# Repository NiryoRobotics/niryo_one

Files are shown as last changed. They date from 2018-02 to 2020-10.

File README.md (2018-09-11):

# Niryo One

(Niryo One : [https://niryo.com](https://niryo.com/?utm_source=github))

Niryo One image

This repository contains STL files to print Niryo One with a 3D printer.

Note : **You need at least a 200mm\*200mm\*200mm 3D printer to be able to print all the parts.**

You can find Niryo One ROS stack here : https://github.com/NiryoRobotics/niryo_one_ros 

Enjoy !

---

Note : if you have received your Niryo One before September 2018, the files related to your robot are located in the "Archive (v 1.1.0)" folder.

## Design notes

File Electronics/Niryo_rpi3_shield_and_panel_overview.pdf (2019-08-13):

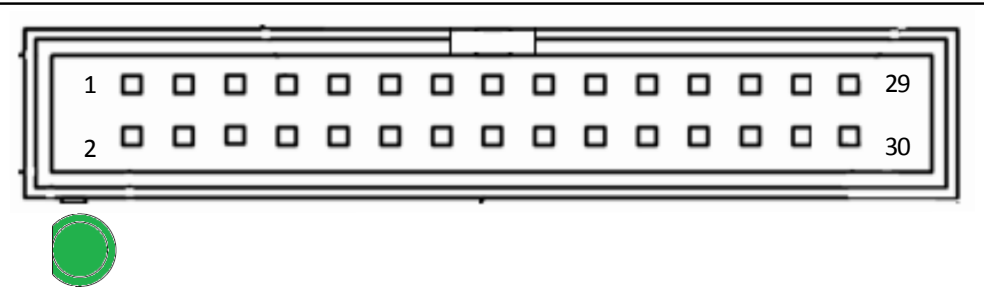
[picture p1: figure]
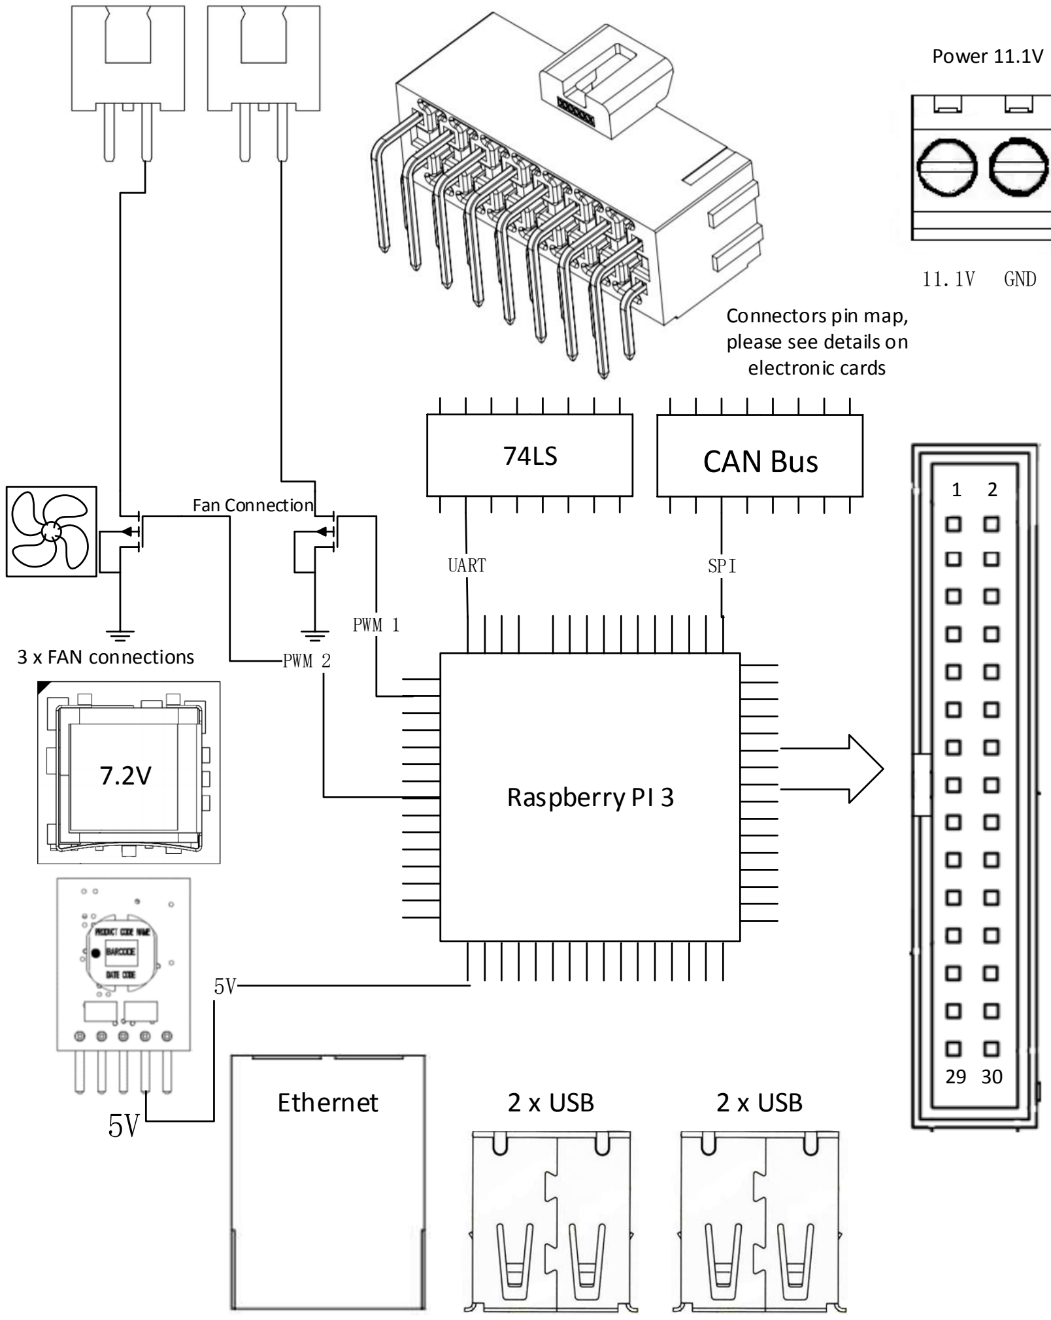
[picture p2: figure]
Raspberry PI 3; CAN Bus ⁷⁴LS; Power 11.1V; 3 x FAN connections; UART; SPI; PWM 2; PWM 1; GND; Fan Connection; Ethernet; 2 x USB; Connectors pin map, please see details on electronic cards

CANH CANL GND 11.1V | GND 7.2V DLX-Data1 | GND 11.1V
CANH CANL GND 11.1V | GND 11.1V

GND 5V 1A(IO2) 1B(IO3) 1C (IO16)

GND 5V 2A(IO26) 2B(IO19) 2C(IO6)
GND 7.2V DLX-Data2

NiryoShield Pin Map

Pin# | Name
01 | 7.2V DC Power
03 | DLX-Data
05 | 11.1V DC Power
07 | 11.1V DC Power
09 | 11.1V DC Power
11 | IO24
13 | GND
15 | GND
17 | GND
19 | GND
21 | 5V DC Power
23 | 5V DC Power
25 | IO2 SDA
27 | IO3 SCL
29 | IO16
Name | Pin#

7.2V DC Power 02

IO18 | 04
11.1V | 06
IO22 | 08
NC | 10
CANL | 12
CANH | 14
NC | 16
NC | 18
NC | 20
NC | 22
NC | 24
IO6 | 26
IO19 | 28
IO26 | 30

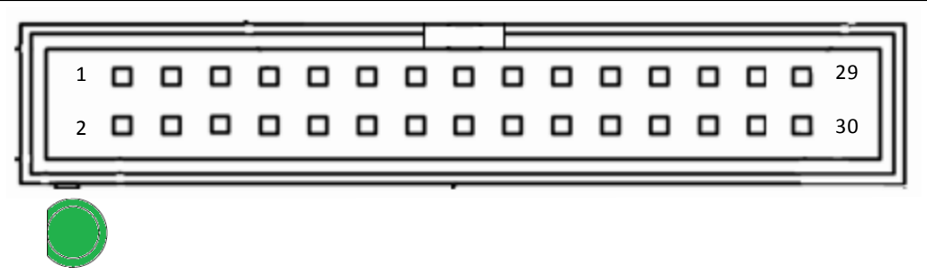
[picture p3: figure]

CANH CANL GND 11.1V GND 7.2V DLX-Data1 | GND 11.1V
CANH CANL GND 11.1V | GND 11.1V

GND 5V 1A(IO2) 1B(IO3) 1C (IO16)

GND 7.2V DLX-Data2 | GND 5V 2A(IO26) 2B(IO19) 2C(IO6)

Niryo Stepper 1

Niryo Stepper 2

XL-320

XL-430

SW1

SW2

GPIO1

GPIO2

## WARNING !

- Niryo Stepper 1 and Niryo Stepper 2 connectors are reserved. Don't use them.
- Only connect Dynamixel XL-320 motors to the XL-320 connector.
- Only connect Dynamixel XL-430 motors to the XL-430 connector.
- DO NOT short-circuit SW1 and SW2 pins.
- Absolute operating voltage of GPIO1 and GPIO2 connectors is 5V. External expander applications must operate at 5V. DO NOT short-circuit 5V and GND pins with any other pins.

! Wrong connection or wrong input voltage could permanently damage the robot or external micro-controller !

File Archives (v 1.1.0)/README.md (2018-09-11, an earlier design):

# Archive files for version 1.1.0

**IMPORTANT: Those files are related to a previous Niryo One hardware version (< September 2018). You are not concerned if you received your robot during or after September 2018.**

This folder contains the STL files, Electronics overview, and BOM for the previous Niryo One hardware version. If you have received Niryo One before September 2018, you can still print, assemble and use this version without any problem.

All the new software updates are retro-compatible with this version. Read [this article](https://niryo.com/2018/09/11/new-hardware-upgrade-for-niryo-one-september-2018/) to know more.

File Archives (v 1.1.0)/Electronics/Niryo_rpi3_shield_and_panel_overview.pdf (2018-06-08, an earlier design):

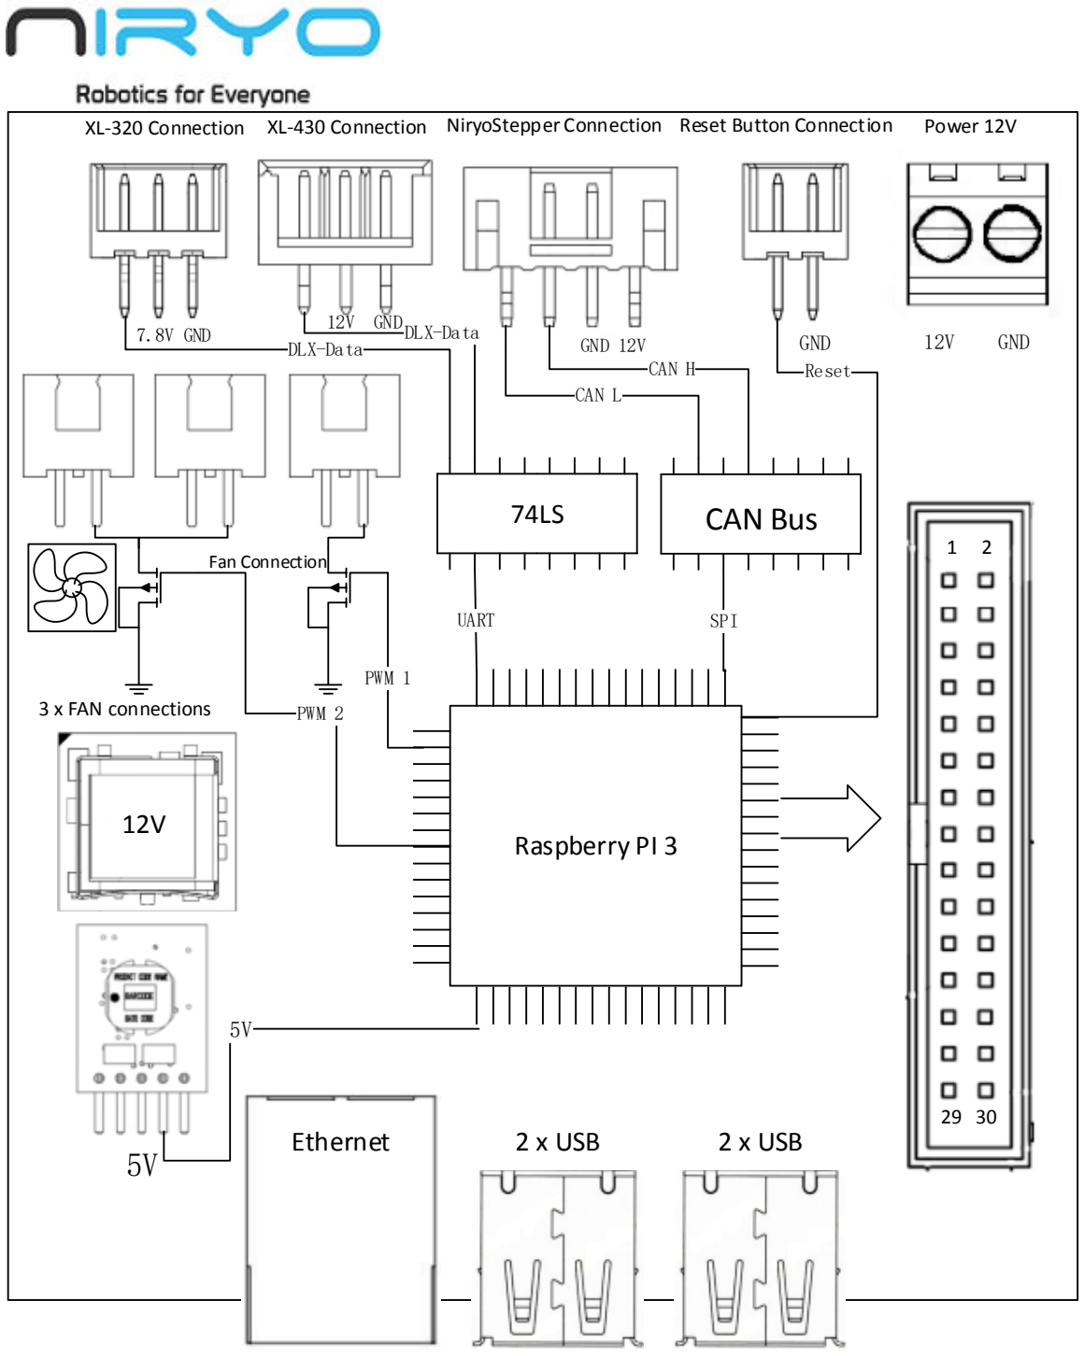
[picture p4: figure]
Raspberry PI 3; CAN Bus ⁷⁴LS; 3 x FAN connections; UART; SPI; DLX-Data; CAN L; CAN H; Reset; PWM 2; PWM 1; GND 12V; GND; GND 7.8V GND; 12V GND; Fan Connection; Ethernet; 2 x USB

XL-320 Connection XL-430 Connection NiryoStepper Connection Reset Button Connection | Power 12V

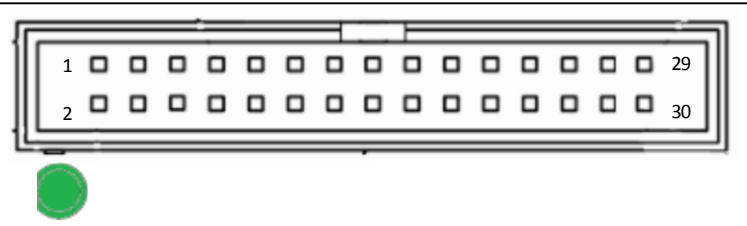
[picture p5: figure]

CANH CAN L GND 12V | GND 7.8V DLX-Data1 | GND 12V
CANH CAN L GND 12V | GND 12V

GND 5V 1A(IO2) 1B(IO3) 1C (IO16)

GND 5V 2A(IO26) 2B(IO19) 2C(IO6)
GND 7.8V DLX-Data2

# NiryoShield Pin Map

Pin# | Name
01 | 7.6V DC Power
03 | DLX-Data
05 | 12V DC Power
07 | 12V DC Power
09 | 12V DC Power
11 | IO24
13 | GND
15 | GND
17 | GND
19 | GND
21 | 5V DC Power
23 | 5V DC Power
25 | IO2 SDA
27 | IO3 SCL
29 | IO16
Name | Pin#

7.6V DC Power 02

IO18 | 04
12V | 06
IO22 | 08
NC | 10
CANL | 12
CANH | 14
NC | 16
NC | 18
NC | 20
NC | 22
NC | 24
IO6 | 26
IO19 | 28
IO26 | 30

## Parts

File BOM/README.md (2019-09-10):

# Niryo One BOM

The BOM\_StepByStep file shows you the BOM for each assembly step.

More resources :
* [Google Sheet containing the detailed Niryo One BOM per category](https://docs.google.com/spreadsheets/d/e/2PACX-1vQf0Kui9UcmFLxmP--nyz-DuXEQUxWGpeM21uyZKIYzpjAP0tSZv4hCnaOMoByFpGlYtLtWEO1d9n8G/pub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)
* [Niryo One Assembly guide](https://niryo.com/docs/niryo-one/assembly-guide/assemble-niryo-one/)

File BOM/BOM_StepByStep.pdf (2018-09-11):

# Niryo One BOM step by step (following Assembly guide)

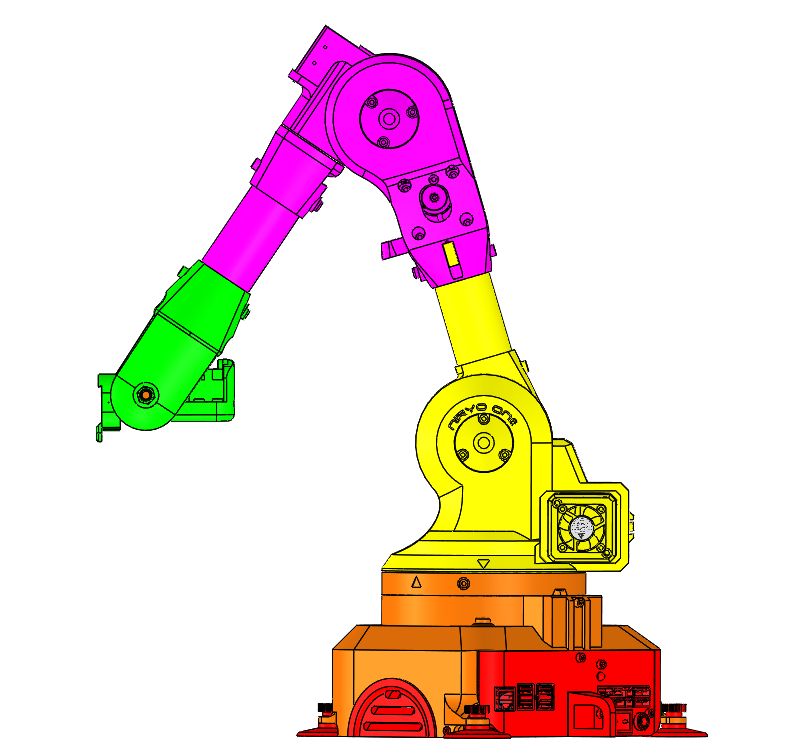
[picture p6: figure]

# 1 - Base

# 2 - Shoulder

# 3 - Elbow

# 4 - Wrist

# 5- Drawer

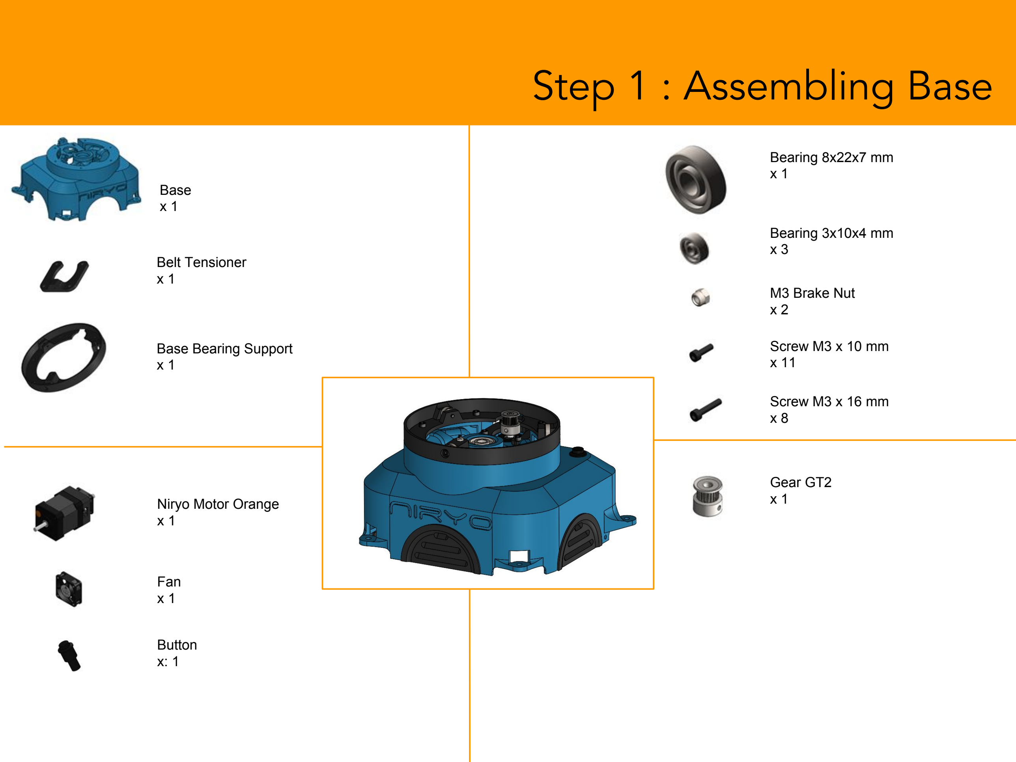
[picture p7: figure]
Step 1 : Assembling Base; Base x 1; Belt Tensioner x 1; Base Bearing Support x 1; Fan x 1; Button x: 1; Niryo Motor Orange x 1; Bearing 3x10x4 mm x 3; Bearing 8x22x7 mm x 1; M3 Brake Nut x 2; Screw M3 x 10 mm x 11; Screw M3 x 16 mm x 8; Gear GT2 x 1

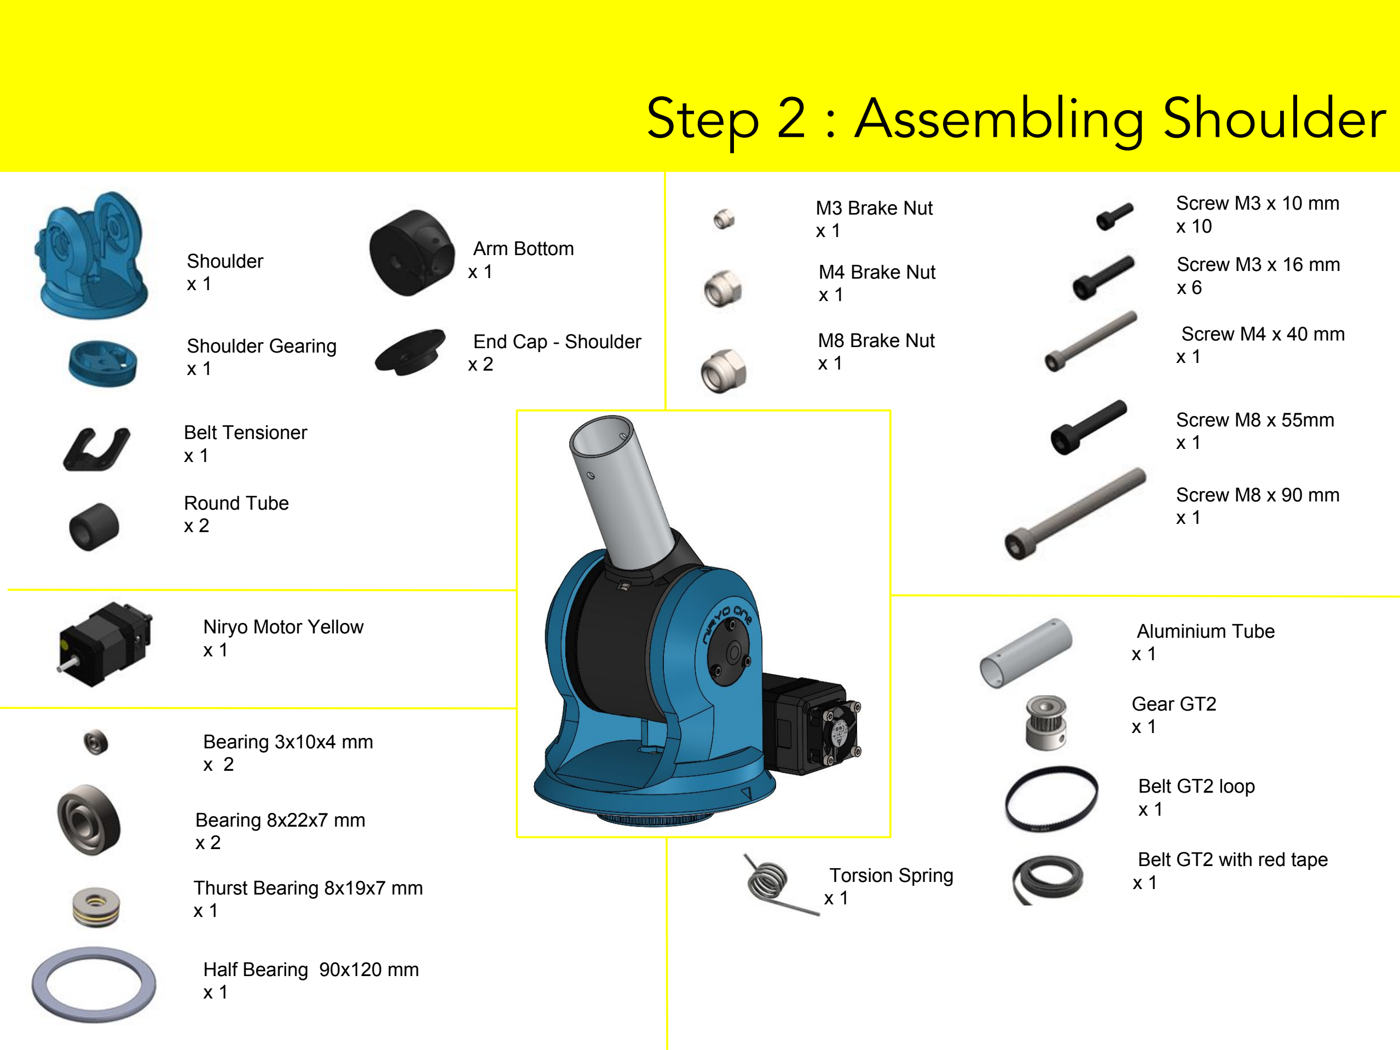
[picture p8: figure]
Step 2 : Assembling Shoulder; Shoulder x 1; Shoulder Gearing x 1; Belt Tensioner x 1; Bearing 3x10x4 mm x 2; Thurst Bearing 8x19x7 mm x 1; Niryo Motor Yellow x 1; M8 Brake Nut x 1; M3 Brake Nut x 1; Half Bearing 90x120 mm x 1; Belt GT2 loop x 1; Gear GT2 x 1; Bearing 8x22x7 mm x 2; End Cap - Shoulder x 2; Belt GT2 with red tape x 1; Round Tube x 2; Screw M4 x 40 mm x 1; M4 Brake Nut x 1; Aluminium Tube x 1; Arm Bottom; Screw M3 x 16 mm; Screw M3 x 10 mm x 10; Screw M8 x 55mm x 1; Screw M8 x 90 mm x 1; Torsion Spring x 1

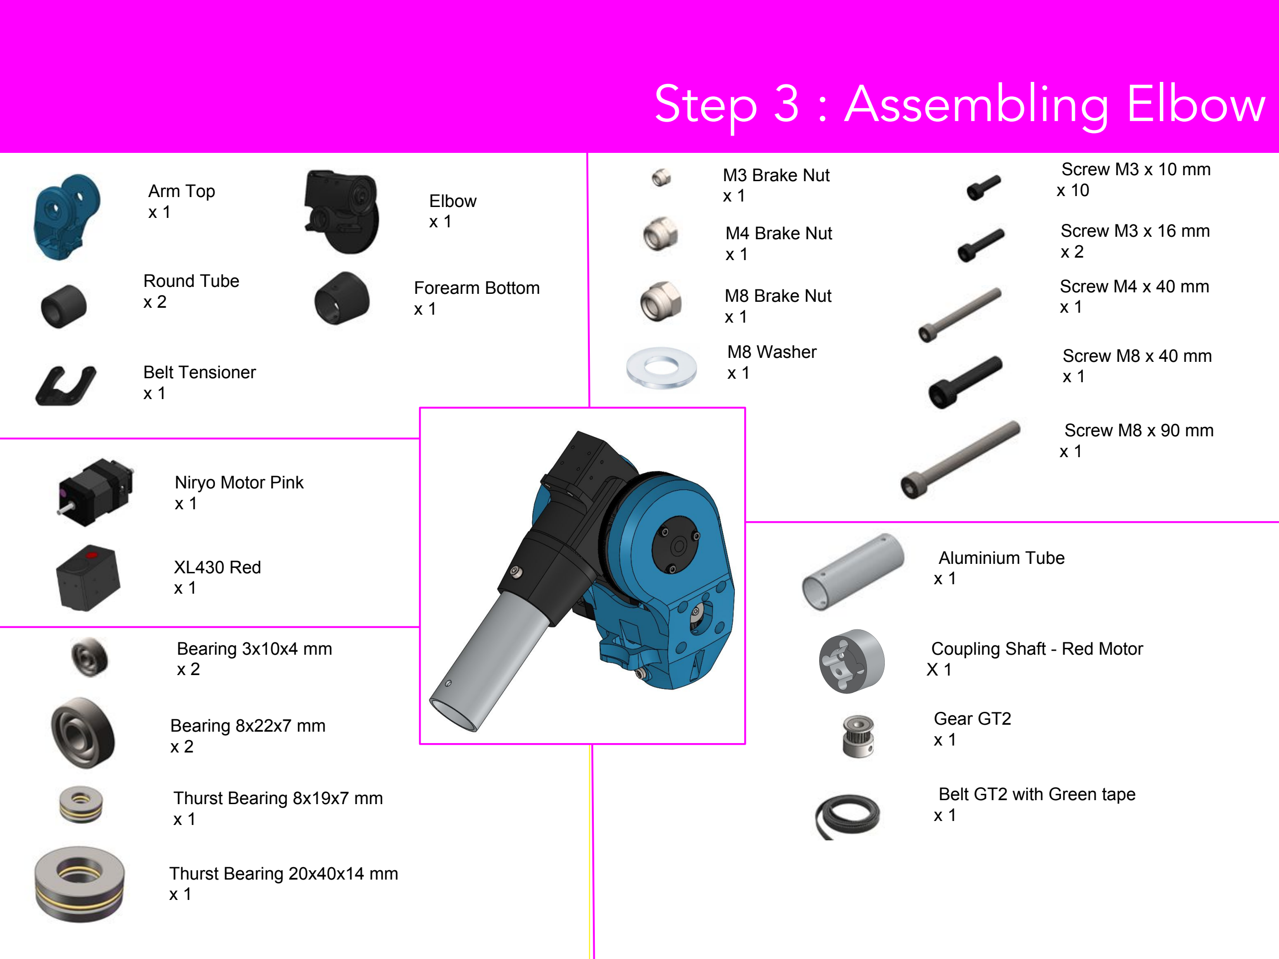
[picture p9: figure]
Step 3 : Assembling Elbow; Bearing 3x10x4 mm x 2; Screw M3 x 16 mm x 2; Screw M3 x 10 mm x 10; Gear GT2 x 1; Arm Top x 1; Belt Tensioner x 1; Belt GT2 with Green tape x 1; Niryo Motor Pink x 1; Bearing 8x22x7 mm x 2; Coupling Shaft - Red Motor X 1; Round Tube x 2; M8 Washer x 1; Forearm Bottom x 1; Elbow x 1; Screw M4 x 40 mm x 1; Aluminium Tube x 1; Screw M8 x 90 mm x 1; Screw M8 x 40 mm x 1; Thurst Bearing 20x40x14 mm; Thurst Bearing 8x19x7 mm x 1; M8 Brake Nut x 1; M3 Brake Nut x 1; M4 Brake Nut x 1; XL430 Red x 1

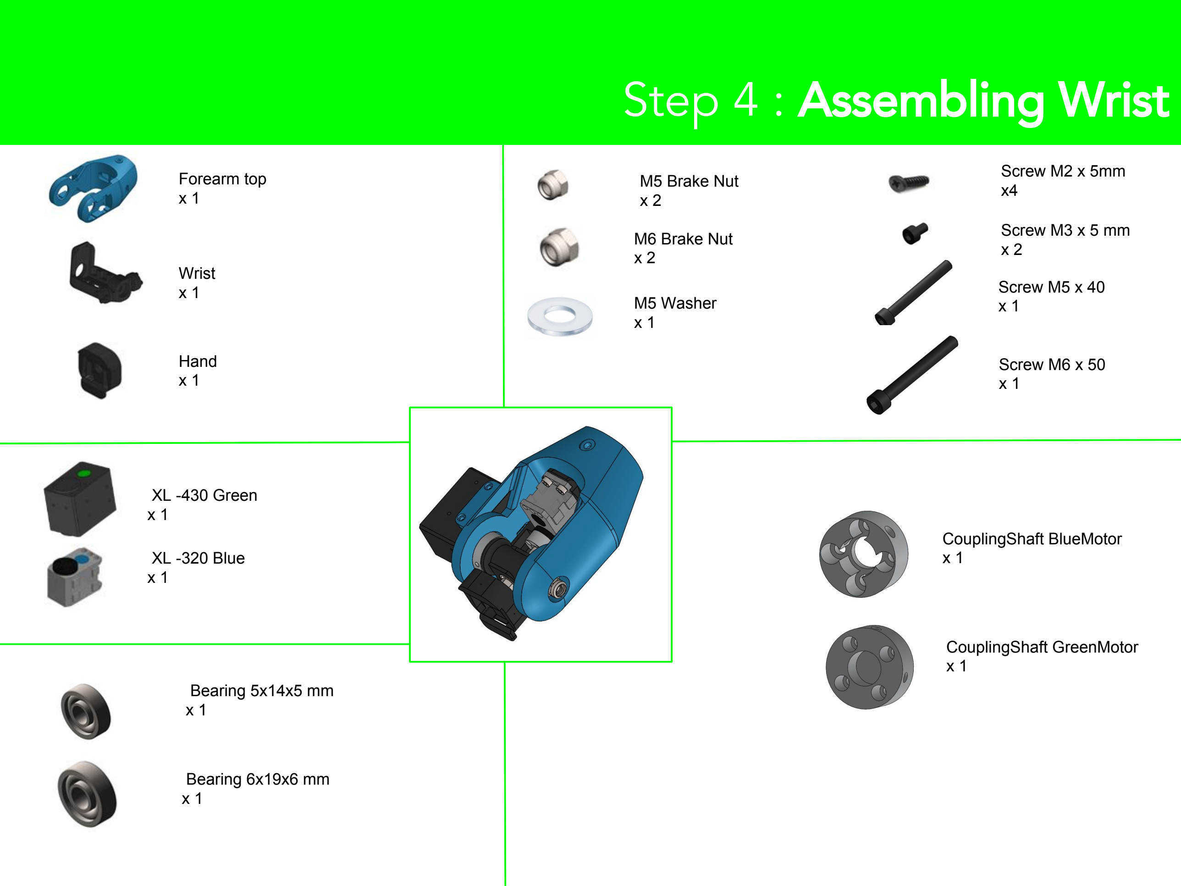
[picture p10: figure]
Step 4 : Assembling Wrist; M5 Brake Nut x 2; Wrist x 1; Hand x 1; Forearm top x 1; XL -320 Blue x 1; Screw M3 x 5 mm x 2; Screw M2 x 5mm x4; Bearing 6x19x6 mm x 1; Bearing 5x14x5 mm x 1; CouplingShaft GreenMotor x 1; CouplingShaft BlueMotor x 1; M5 Washer x 1; Screw M5 x 40 x 1; Screw M6 x 50 x 1; M6 Brake Nut x 2; XL -430 Green x 1

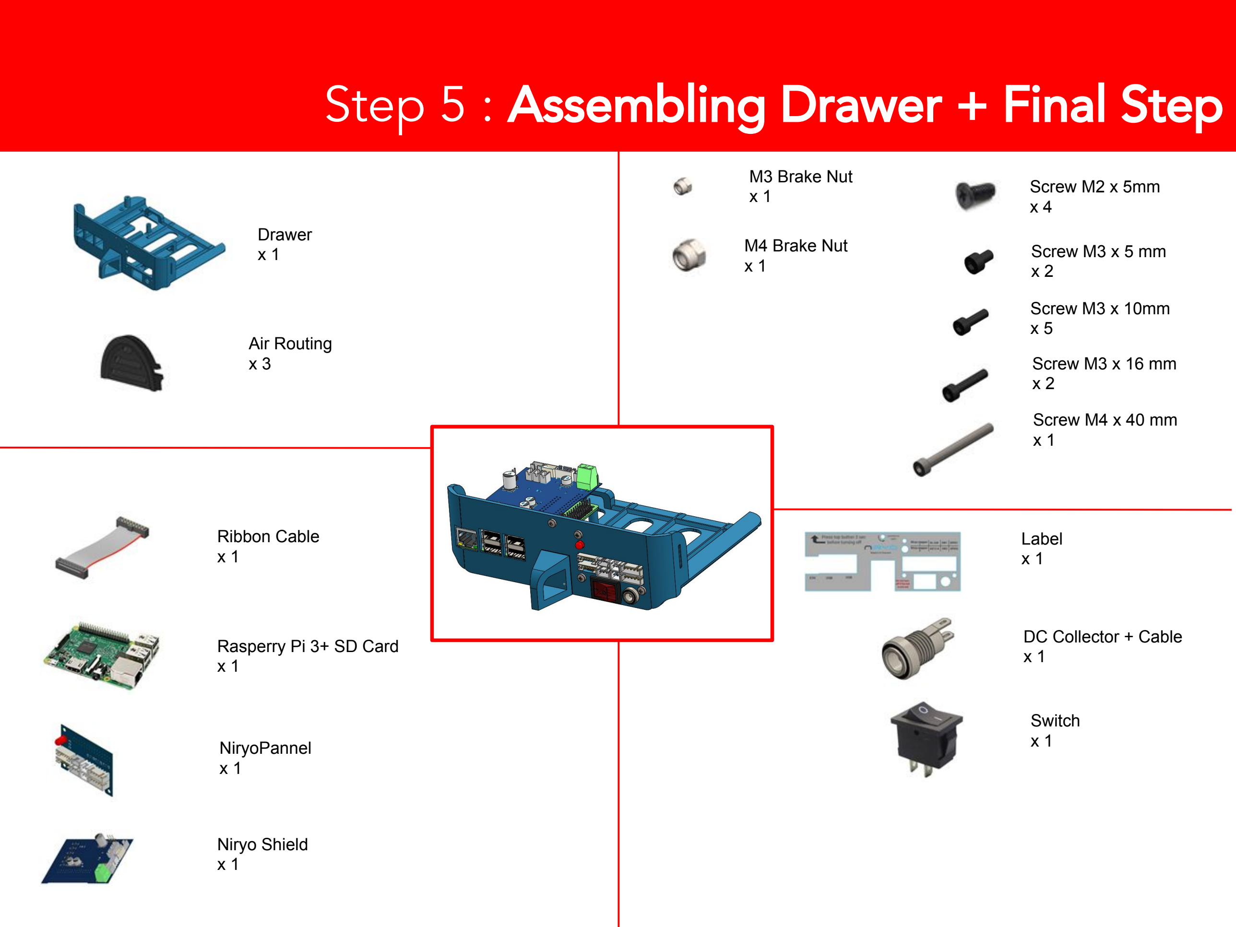
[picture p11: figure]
Step 5 : Assembling Drawer + Final Step; Drawer x 1; Ribbon Cable x 1; Rasperry Pi 3+ SD Card x 1; NiryoPannel x 1; Niryo Shield; Label x 1; DC Collector + Cable x 1; Switch x 1; Screw M3 x 10mm x 5; Screw M2 x 5mm x 4; Screw M3 x 16 mm x 2; Screw M3 x 5 mm x 2; Air Routing x 3; Screw M4 x 40 mm x 1; M3 Brake Nut x 1; M4 Brake Nut x 1

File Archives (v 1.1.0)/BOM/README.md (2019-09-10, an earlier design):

# Niryo One BOM

You can find a Google Sheet containing the detailed Niryo One BOM [here](https://docs.google.com/spreadsheets/d/e/2PACX-1vQdaiK_vy_xeSN82euNUj4mnmYRxMGzbDUkNO7cfYsx0wwn-GCbwwnOM1JslDBoyodkNQlpweZOdBDd/pub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).

The BOM\_StepByStep file shows you the BOM for each assembly step.

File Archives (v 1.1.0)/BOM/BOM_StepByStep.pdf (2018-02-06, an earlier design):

# Step1 : Assembling Base

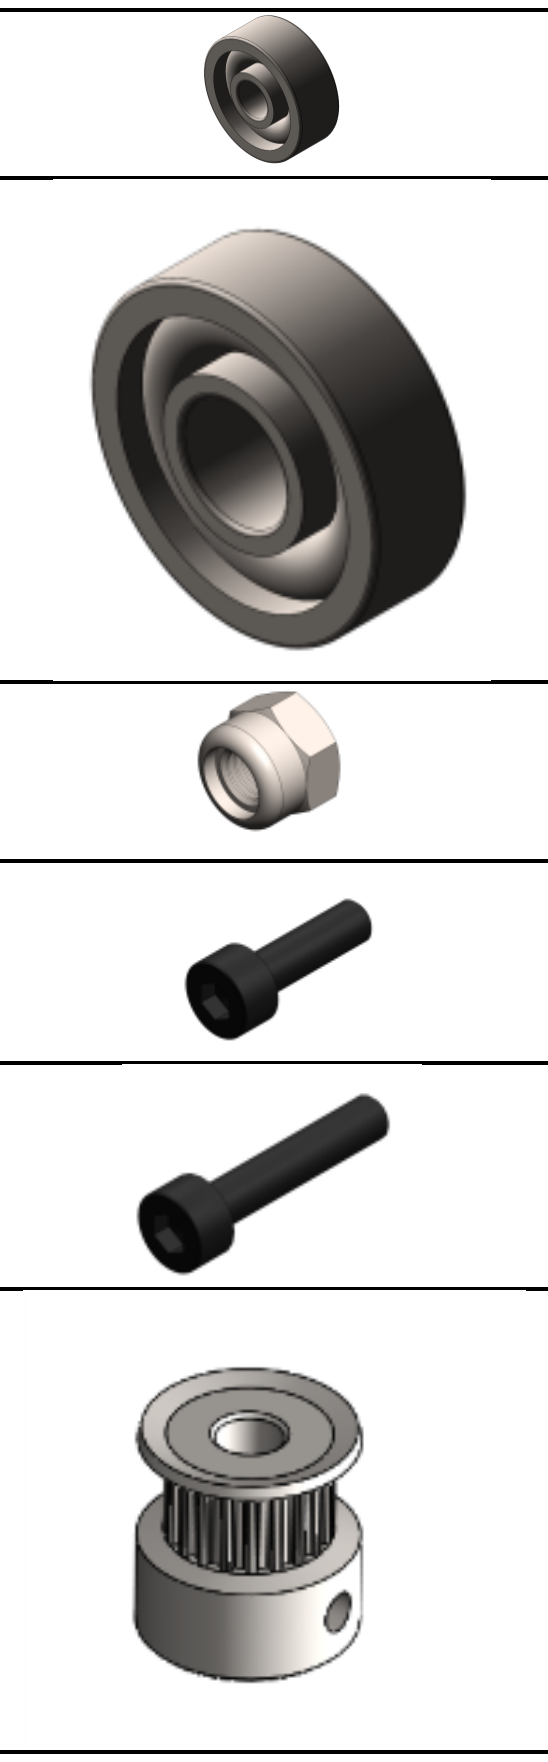
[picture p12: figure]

Bearing 3x10x4 mm | 3

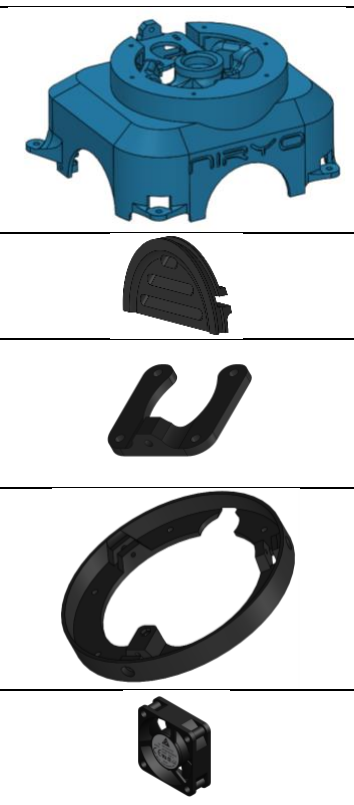
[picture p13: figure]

Bearing 8x22x7 mm | 1
M3 Brake Nut | 2
Screw M3 x 10 mm | 11
Screw M3 x 15 mm | 5
Gear GT2 | 1
Picture | Name | Number
Base | 1
Air Routing | 3
Belt tensioner | 1
Base Bearing Support | 1
Fan | 1
Switch | 1
Niryo Motor Orange | 1

# Step2 : Assembling Shoulder


Screw M3 x 10 mm | 4
Screw M3 x 15 mm | 5
Screw M8 x 55 mm | 1
M3 Brake Nut | 1


M8 Brake Nut | 1
Belt GT2 loop | 1
Picture | Name | Number
Shoulder | 1
Shoulder Gearing | 1
Belt tensioner | 1
Niryo Motor Yellow | 1
Wiring 1 & 2 | 1


Bearing 3x10x4 mm | 2
Thurst Bearing 8x19x7 mm | 1
Half Bearing 90x120mm | 1

# Step 3 : Assembling Arm

Picture | Name | Number


Arm Bottom | 1
Arm Top | 1
Round Tube | 2
Belt tensioner | 1
Belt GT2 with red tape | 1
Screw M8 x 90 mm | 1
Screw M4 x 40 mm | 2
Screw M3 x 15 mm | 1
Screw M3 x 10 mm | 4
M8 Brake Nut | 1
M4 Brake Nut | 2
M3 Brake Nut | 1
Bearing 8x22x7 mm | 2
Bearing 3x10x4 mm | 2
torsion spring | 1
Gear GT2 | 1
Aluminium Tube | 1
Niryo Motor Pink | 1

# Step 4 : Assembling Elbow + Forearm Bottom


Picture | Name | Number


Elbow | 1
Forearm Bottom | 1
Round Tube | 2
Niryo Motor Red | 1
Gear GT2 | 1
Belt tensioner | 1
Belt GT2 | 1

Thurst Bearing
20x40x14 mm

1

Thurst Bearing 8x19x7 mm | 1
Bearing 8x22x7 mm | 2
Screw M8 x 90 mm | 1
Screw M8 x 40 mm | 1
Screw M3 x 15 mm | 2
Screw M3 x 10 mm | 3
M8 Brake Nut | 3
M3 Brake Nut | 1

# Step 5 : Assembling Forearm Top + Wrist


Picture | Name | Number


| Forearm Top | 1
| Wrist | 1
| Hand | 1
| Servo Head | 1
| XL -320 Green A & B | 2
| XL -320 Blue | 1
| Cable XL 320 – 80 mm | 2
| Wiring 4 | 1
Aluminium Tube | 1
Bearing 5x14x5 mm | 2
Screw M5 x 35 mm | 1
Screw M4 x 40 mm | 2
Screw M3 x 5 mm | 6
Screw m2 x 10mm | 2
M5 Brake Nut | 3
M4 Brake Nut | 2

# Step 6 : Assembling End

Picture | Name | Number


| End Cap - Shoulder | 2
| End Cap - Arm | 2
| Screw M3 x 15 mm | 6

# Step 7 : Assembling Drawer


DC connector +
cable | 1
Switch | 1
Screw M3 x 10 mm | 5
Screw M2 x 5 mm | 4
M3 Brake Nut | 3
Picture | Name | Number
Drawer | 1
Ribbon cable | 1


Raspberry Pi 3 + SD Card | 1
Niryo-Pannel | 1
Niryo-Shield | 1
Label | 1

# G1 : Assembling Gripper 1


G_Cable | 1
Screw M3 x 10 mm | 4
Screw M3 x 5 mm | 2
Screw M2 x 5 mm | 2
Rubber | 1
Picture | Name | Number
G1_MainSupport | 1
G1_ClampLeft | 1
G1_ClampRight | 1
G1_ServoHead | 1
G1_Rod | 2
XL -320 White | 1

# G2 : Assembling Gripper 2


XL -320 Grey | 1
G_Cable | 1
Screw M3 x 20 mm | 6


Screw M3 x 15 mm | 1
Screw M3 x 5 mm | 2
Screw m2 x 10mm | 2
Bearing 3x10x4 mm | 14
M3 Brake Nut | 6
Rubber | 1
Picture | Name | Number
G2_MainSupport | 1
G2_GearLeft | 1
G2_GearRight | 1
G2_Rod | 2
G2_Clamp | 2

# G3 : Assembling Gripper 3


Picture | Name | Number


G3_Main Support | 1
G3_GearRight | 1
G3_GearLeft | 1
G3_Link1 | 2
G3_Link2 | 2
G3_Rod | 2
XL -320 Black | 1
G_Cable | 1
Screw M3 x 20 mm | 8
Screw M3 x 15 mm | 1
Screw M3 x 5 mm | 2
Screw m2 x 10mm | 2
Bearing 3x10x4 mm | 18
M3 Brake Nut | 8
G3_Spring | 2
Rubber | 1

# EM : Assembling Electro Magnet

Picture | Name | Number
| EM_Main Support | 1
| ElectroMagnet Grove | 1
| Screw M2 x 5 mm | 2
| EM_Cable | 1

# VP : Assembling Vacuum Pump


VP_Suction Cup | 1
VP_Plastic Elbow | 1
VP_Flexible | 1
Syringe | 1
Screw M3 x 10 mm | 3
Screw M3 x 5 mm | 2
Cable XL 320 – 60 mm | 1
Picture | Name | Number
VP_Main Support | 1
VP_ Hood | 1
VP_ServoHead | 1
VP_SyringeHolder | 1
VP_Link | 1
VP_ SuctionCup Support | 1

# PH : Assembling Pen Holder

Picture | Name | Number


| PH_MainSupport | 1
| PH_Inside | 1
| PH_Head | 1
| PH_Spring | 2
| Screw Butterfly | 1

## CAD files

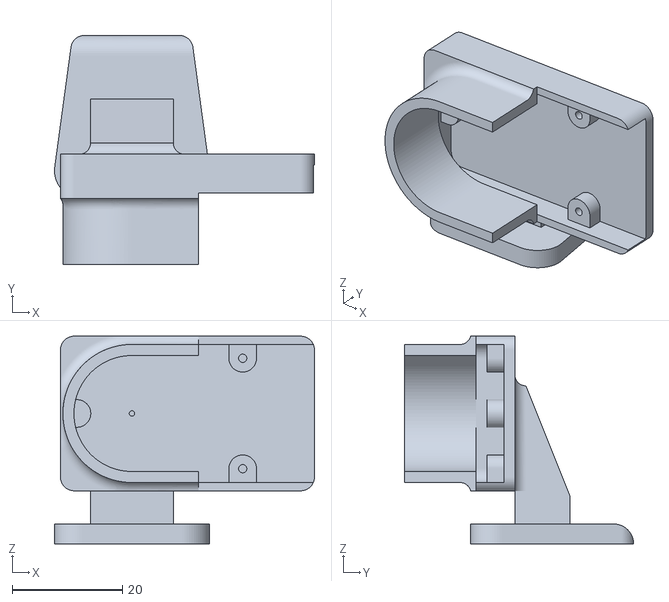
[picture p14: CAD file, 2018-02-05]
STL/7-Tools/Electromagnet/EM_Main Support.STL
47.1 x 41.5 x 37.6

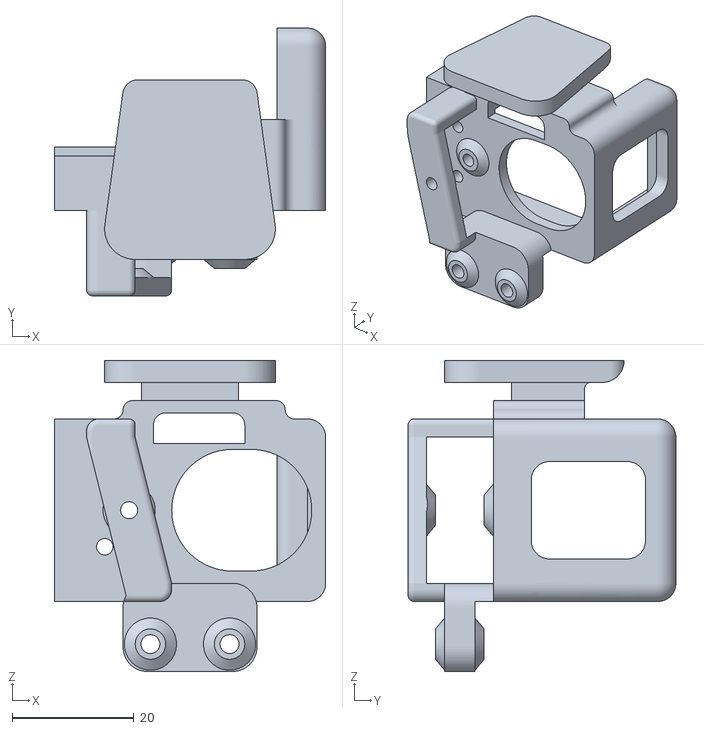
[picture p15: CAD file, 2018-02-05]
STL/7-Tools/Gripper2/G2_MainSupport.STL
44.6 x 44.0 x 51.1

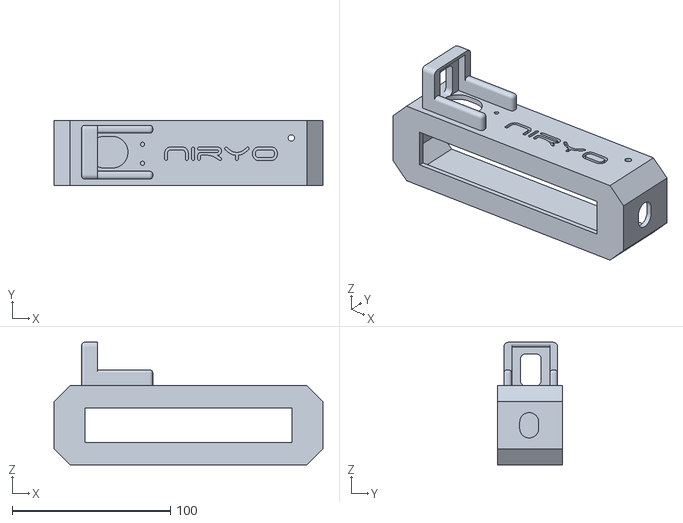
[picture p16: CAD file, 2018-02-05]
STL/7-Tools/VacuumPump/VP_MainSupport.STL
170.0 x 41.0 x 77.5

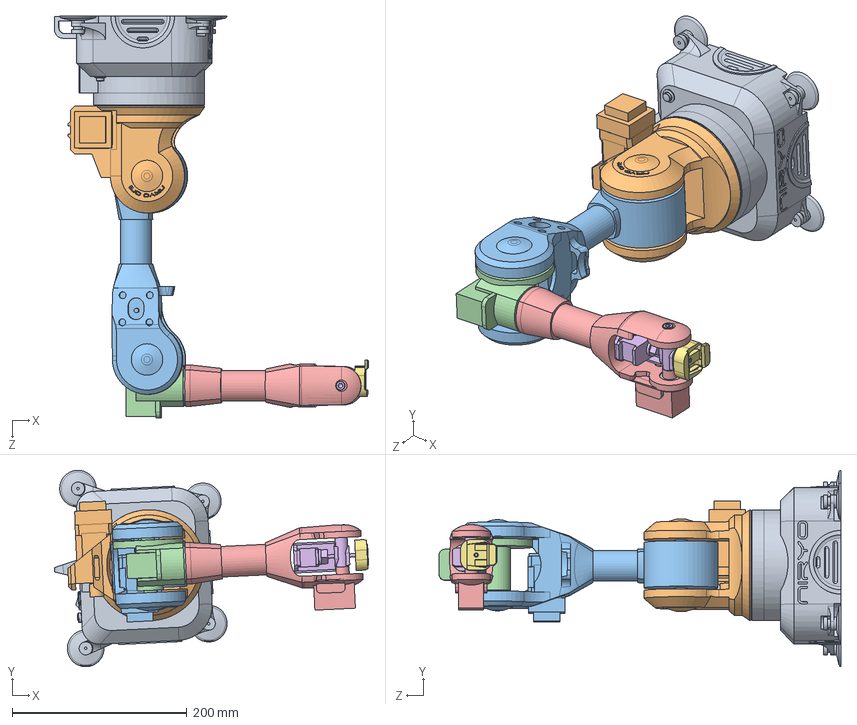
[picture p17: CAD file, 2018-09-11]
Integration/Solidworks/NiryoOneSimplifie.SLDASM
359.5 x 224.8 x 460.0 mm
1-Base_NiryoOne_V2.0
2-Shoulder_NiryoOne_V2.0
3-Arm_NiryoOne_V2.0
4-Elbow_NiryoOne_V2.0
5-Forearm_NiryoOne_V2.0
6-Wrist_NiryoOne_V2.0
7-Hand_NiryoOne_V2.0

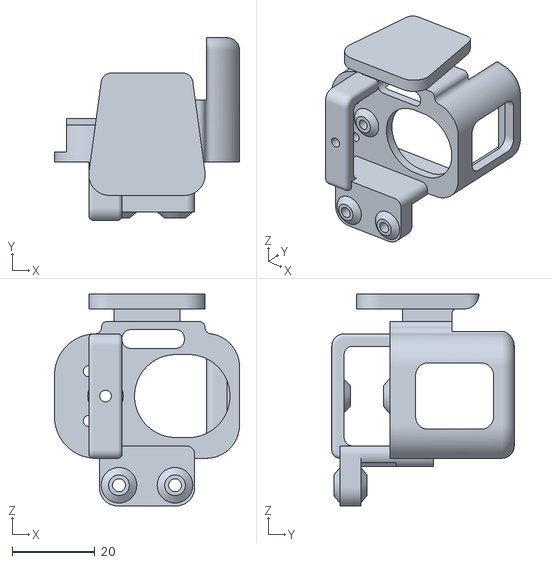
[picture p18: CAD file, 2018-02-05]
STL/7-Tools/Gripper3/G3_MainSupport.STL
44.6 x 44.0 x 51.1

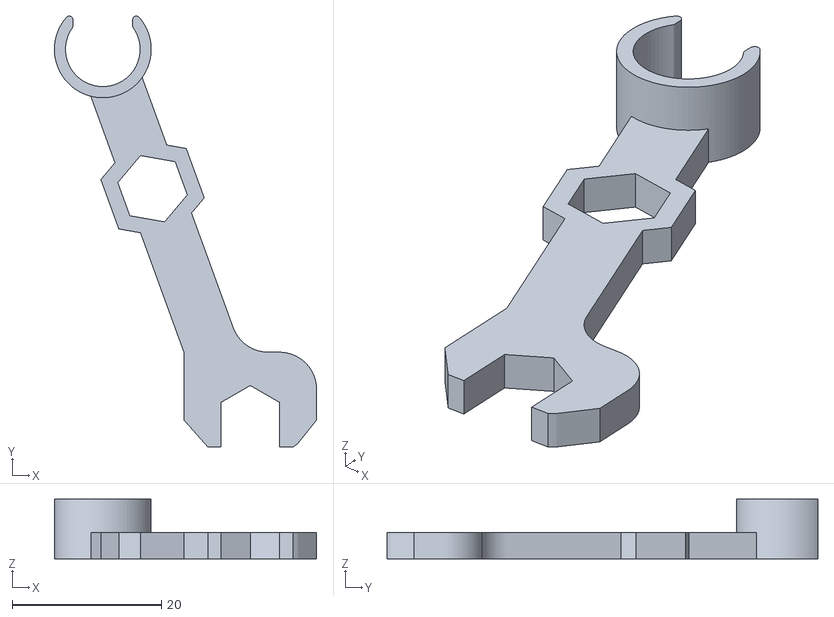
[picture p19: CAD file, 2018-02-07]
STL/8-Other/AssemblyTool2.STL
35.2 x 57.8 x 8.00

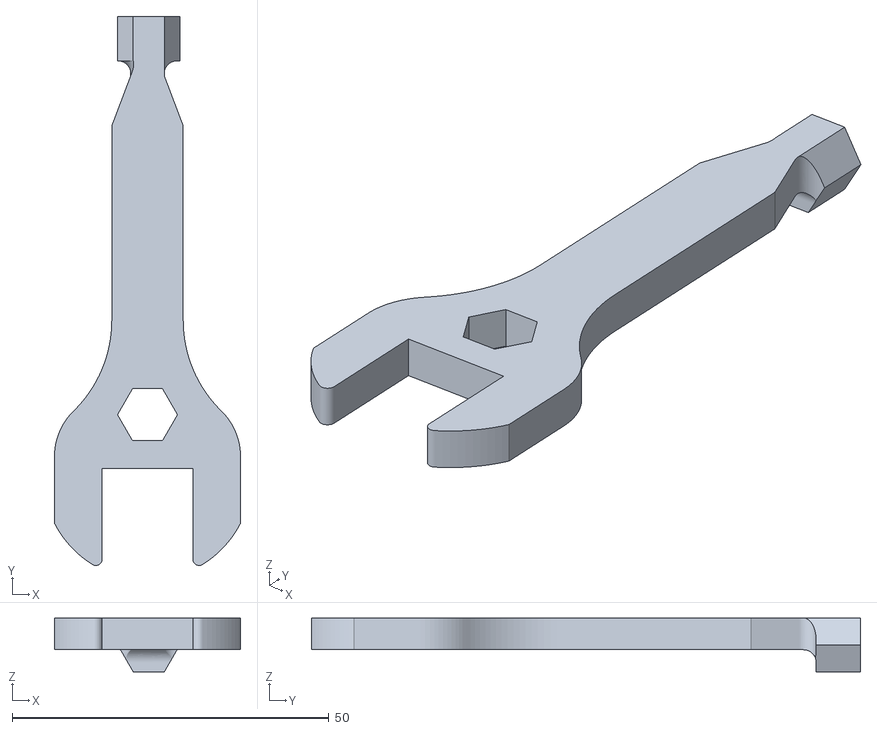
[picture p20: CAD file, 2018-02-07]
STL/8-Other/AssemblyTool1.STL
29.4 x 86.7 x 8.50

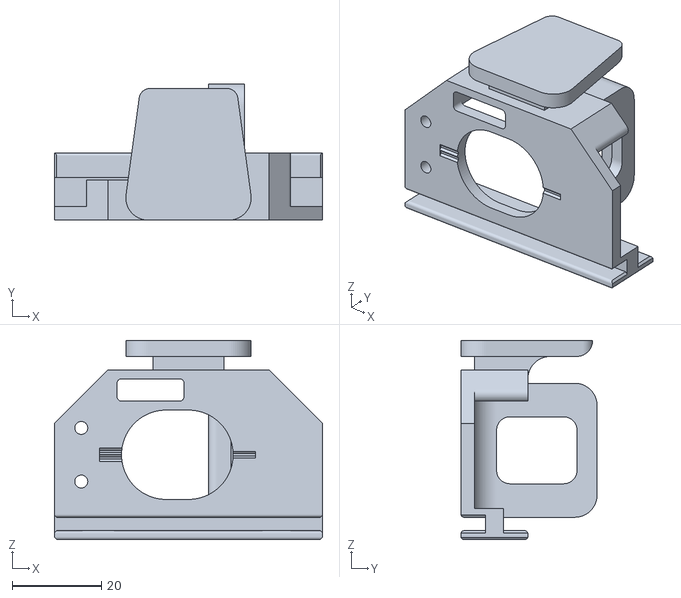
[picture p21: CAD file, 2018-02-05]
STL/7-Tools/Gripper1/G1_MainSupport.STL
60.0 x 30.5 x 44.6

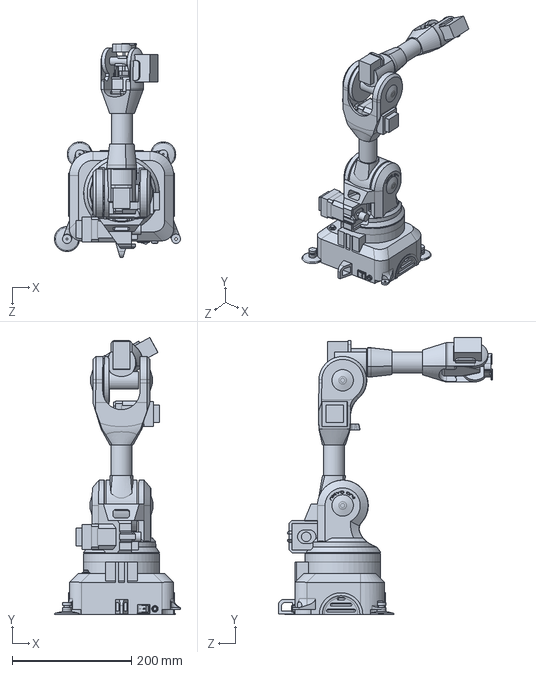
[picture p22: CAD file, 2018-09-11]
Integration/Solidworks/NiryoOne_V2.0.SLDPRT
211.5 x 464.8 x 359.7 mm

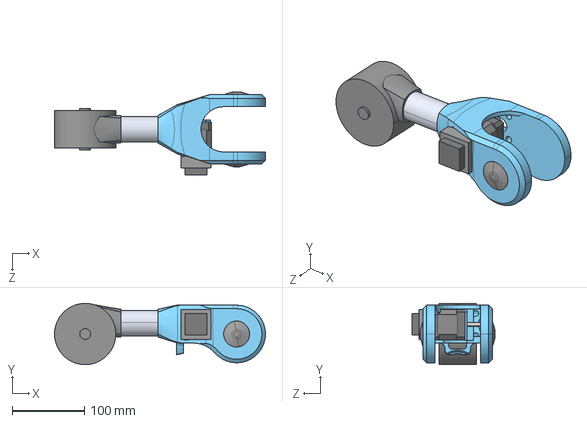
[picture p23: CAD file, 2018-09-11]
Integration/STEP/3-Arm_NiryoOne_V2.0.STEP
292.5 x 85.0 x 115.7 mm

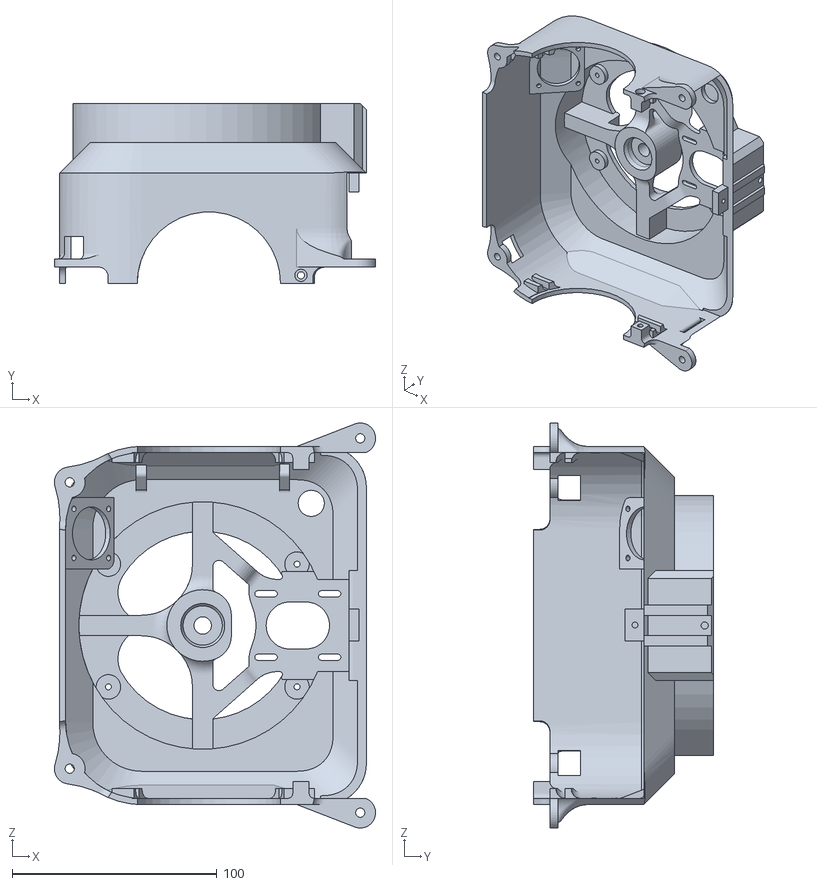
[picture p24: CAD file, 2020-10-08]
STL/0-Base/Base.STL
157.0 x 88.0 x 198.0

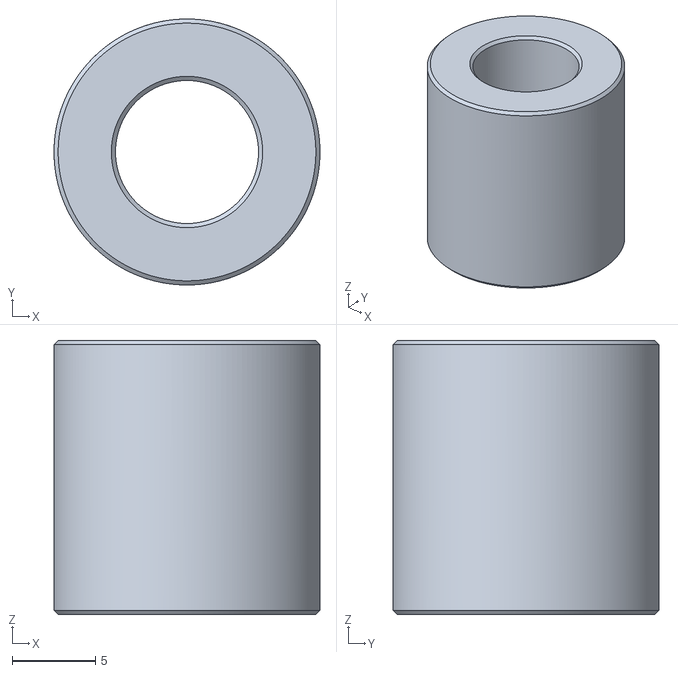
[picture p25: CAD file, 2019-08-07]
STL/1-Shoulder/RoundTube.STL
16.0 x 16.0 x 16.5

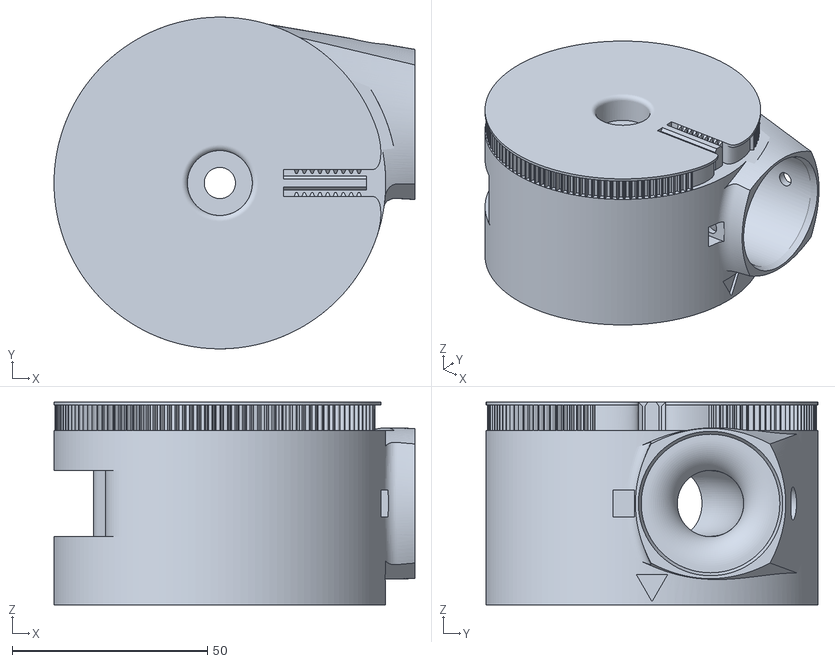
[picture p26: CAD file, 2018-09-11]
STL/2-Arm/ArmBottom.STL
92.5 x 85.0 x 52.0

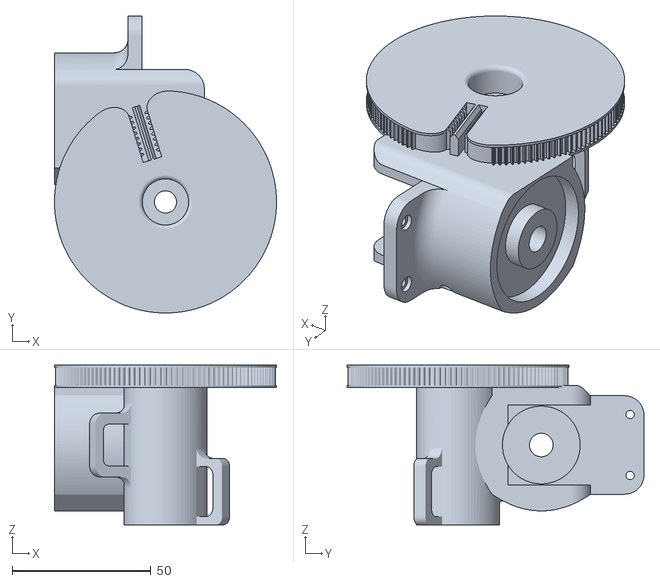
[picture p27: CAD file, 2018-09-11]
STL/3-Elbow/Elbow.STL
80.0 x 107.0 x 57.6

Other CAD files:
STL/4-ForeArm/ForeArmBottom.STL
STL/5-Wrist/Wrist.STL
STL/6-Hand/Hand.STL
STL/7-Tools/Gripper1/G1_ClampRight.STL
Archives (v 1.1.0)/STL/1-Base/Air routing.STL
Archives (v 1.1.0)/STL/1-Base/Base bearing support.STL
Archives (v 1.1.0)/STL/1-Base/Base.STL
Archives (v 1.1.0)/STL/1-Base/Drawer-RaspberryPi.STL
Archives (v 1.1.0)/STL/2-Shoulder/End Cap - Shoulder.STL
Archives (v 1.1.0)/STL/2-Shoulder/Round tube.STL
Archives (v 1.1.0)/STL/2-Shoulder/Shoulder gearing.STL
Archives (v 1.1.0)/STL/2-Shoulder/Shoulder.STL
Archives (v 1.1.0)/STL/3-Arm/Arm-Bottom.STL
Archives (v 1.1.0)/STL/3-Arm/Arm-Top.STL
Archives (v 1.1.0)/STL/3-Arm/End Cap - Arm.STL
Archives (v 1.1.0)/STL/4-Elbow/Elbow.STL
Archives (v 1.1.0)/STL/5-Forearm/Forearm-Bottom.STL
Archives (v 1.1.0)/STL/5-Forearm/Forearm-Top.STL
Archives (v 1.1.0)/STL/6-Wrist/Servo head.STL
Archives (v 1.1.0)/STL/6-Wrist/Wrist.STL
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

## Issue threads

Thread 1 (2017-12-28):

List of not print parts

photo-mickey, 2017-12-28:
Hello!

Can you share the list of not print parts?
Can I buy your custom electronics parts? I mean adaptor for Raspberry pi and Arduino controllers for steppers. Or maybe you can share the PCB and list of components.

renarded, 2018-01-05:
Hi,

We plan to sell the custom electronics parts from March, 2018.

We'll also update this repository with more info about schematics, list of parts, assembly guide, tutorials, etc :)

photo-mickey, 2018-01-09:
Thank you. I will wait for it ;) If i have understood correctly, I should wait for new stl too.

Jean8marc, 2018-02-06:
Bonjour,
J'espère que la mise a jour des fichiers imprimables va bientôt arriver. Il me tarde de commencer.

renarded, 2018-02-06:
Hi,

All STL files have been updated (+ tools), and we also add the complete list of materials in the BOM folder. (an assembly video tutorial will be published soon on our website)

You can now print the V 1.0 Niryo One :)

Closed 2018-02-06.

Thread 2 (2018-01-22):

previous version stl files

cool45, 2018-01-22:
Hello niryo robotics team I would like to ask where I can find the 3d models for the older servo design as I already do have a lot of servos from previous robotics projects .Thank You for your time :)
,kya lynch

renarded, 2018-01-29:
Hi,

Sorry but this version is not available (and I don't think we can even find it, because we changed it a lot and started to keep strong version archives not so long ago). We will keep updating the current version and published future versions, but not past ones.

The older servo design was dropped for good reasons to switch to Dynamixel XL-320. ([Here](https://www.kickstarter.com/projects/niryo/niryo-one-an-open-source-6-axis-robotic-arm-just-f/posts/1859166) is the update news)

In the meantime we have modified all the other parts of the robot a lot, and the version we've just published is the first stable version. So if you have the version from one year ago, you won't be able to do anything with it. The code on the electronics boards won't work, the dimension of the robot will be wrong, and you'll face heat issues on the motors.

I hope you understand !

jerinpeter, 2019-07-10:
sir is there any way we can get the stl file of fore arm top with the compatibility of normal servos, please do help sir i have spend a loot of time 3d printing the parts and found this out at last thinking that it was backward compatible. can you please please help me... i have been working on this for a month now, as i am building from scratch, gathering parts was also a tiresome job. Hope you will help me.

jerin

renarded, 2019-07-11:
Hi,

Unfortunately the answer I previously provided earlier for this discussion stays the same.

The only possibility for you is to use the STEP files and modify them + print 3D parts, so you can build an alternative robot for your own use.

pawaz123, 2024-09-23:
ok sir can you attach the link of step file

Closed 2018-01-29.

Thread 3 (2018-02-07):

BOM

photo-mickey, 2018-02-07:
Hello!

I have some issues about BOM:

1. What is the voltage and size of fan
2. Which switch do you use?
3. What is the size of aluminium tube?
4. Which is diameters of coupler?
5. Which is diametor and teeth nomber of  gear GT2
6. Which is length of belts?
7. Which is power of power supply?

Jean8marc, 2018-02-07:
Bonjour,
Tout d'abord , très bon travail : félicitations.
Par contre, je voudrais ajouter a cette liste ci dessus  d'autres points
Ribbon ? combien de pins ?
Wiring 1 & 2 : ?
le premier switch ?
DC connector + cable ?
Les "Niryo" moteurs ? est il possible d'avoir des infos ?

J'ai commencé les impressions , et déjà commander quelques pièces.

photo-mickey, 2018-02-08:
Jean8marc, they wrote, that custom electronik will be sold in March. If I understood right, the steppers has oun PCB with encoder, driver, MCU, fan and CAN transmiter. The red stepper has planet gear box (from pic).
Ribbon - IDC16 (1 to 1) from pic
DC connector like [this](https://ru.aliexpress.com/item/5PCS-LOT-DC-022B-DC-Power-Jack-Socket-dc-connector-Adapter-interface-DC022B-5-5X2-1MM/32800312541.html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,searchweb201602_4_10152_10151_10065_10344_10068_10342_10343_10340_10341_10543_10084_10083_10618_10307_10301_5722313_10313_10059_10534_100031_10103_10624_520_10623_10622_10621_10620_10142_10125,searchweb201603_1,ppcSwitch_5&algo_expid=82093a1f-df77-4c6b-bbb6-6b943442e939-14&algo_pvid=82093a1f-df77-4c6b-bbb6-6b943442e939&transAbTest=ae803_5&priceBeautifyAB=0). You will choose connector after coosing power supply.

renarded, 2018-02-13:
Hi,

We have taken all your questions, and will try to answer them in the next tutorial/video we will publish over the last few weeks. I will close this issue once the tutorials are published.

The Niryo Steppers contains a stepper motor (NEMA) with a magnet on the back, a custom shield where we use AS5600 sensor to get the position, an ATSAMD21G18 microcontroller (same as on Arduino M0), and a MCP2515 for SPI to CAN connection.

photo-mickey, 2018-02-13:
Ok, thank you!
Unfortunately, answers to these questions are wery important for purchase of components.

Why are use SPI to CAN (not USART to CAN)? It isn't critics.

Agent-Cain, 2018-03-15:
Is there a date for the update of the BOM ?
Can I already begin to print the things or will there be major changes in the .stl files ?

AJakob1983, 2018-04-02:
What about the length of the belt loop and aluminium tube?

Do you have some specifications for the torsion spring?

renarded, 2018-04-03:
Hi everyone,

Sorry for the late reply. We've just published an updated BOM on a Google Sheet, and provided the [link](https://docs.google.com/spreadsheets/d/e/2PACX-1vS6EmT4n43JWafJPHNZq2qyIoZx4T4H3hvxoW7IlD-_LJswFsSpjLghzwzgzjj_bPZjsMo5IDen6eoL/pubhtml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) in this repo. All the questions asked here have been taken into account :)

@photo-mickey We used SPI to CAN because we were already using the UART pins of the Raspberry Pi 3 for the Dynamixel Bus communication (see schematics [here](http://support.robotis.com/en/product/actuator/dynamixel_x/xl-series_main.htm))

photo-mickey, 2018-04-05:
Hello!
1. There is no pic in doc
2. "Gear GT2 : 16 teeths" - diametor is 5mm?
3. "Half Thurst Bearing" - what is it?
4. Do you have any wire drawings?

Closed 2018-04-03.

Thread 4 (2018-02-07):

stl assemblies

smaassen, 2018-02-07:
Hi,

Is it possible to get the `.stl` assemblies of the different part and maybe one assembly of the entire robot? My specific application needs the dimensions of the gripper assembly in order to get the transformation from hand to gripping point. It is quite tedious to near impossible to assemble the `.stl` parts in a cad software (to many faces loaded at once) and measuring it by hand is very uncertain.

I think this will also be useful for the community if they want to design custom parts (custom grippers, sensor mounts, other modifications) Even better would be to publish `.step` files for easier import in CAD software, if you want of go the route of open source. This would still be an abstraction layer to, say Solidworks, parts, since all history of actions is lost.

Best

renarded, 2018-02-13:
Hi,

We are currently working on that, this will be published on this repository soon, so you can fully customize your robot.

renarded, 2018-09-11:
Hi @smaassen,

We have just published the .step files and more useful assembly files under the ["integration" folder](https://github.com/NiryoRobotics/niryo_one/tree/master/Integration).

Closed 2018-09-11.

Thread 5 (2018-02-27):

Electronic layout

RauLasH26, 2018-02-27:
Hi,

Is it possible to get the PCB layout for "Niryo shield" and the pannel with all the parts that I need to build one to myself. It will be nice if you put an electronics quide (which cable goes where)  for this robot. If you can't for this new upgrade version, please do it for the old version the one with the Arduino Mega. Thank you so much, wish you all the best guys!

renarded, 2018-02-27:
Hi,

We'll provide you with basic schematics of the RPi Niryo shield (also the Niryo Stepper boards), so you can see what is connected to what (with RPi GPIOs), and how to use the connections with different devices/cables. This doc is in our TO-DO list, we'll publish it soon. However, we won't release the full PCB file for those boards.

The cables for the old version with Arduino mega is very simple. We used a RAMPS 1.4 shield, with standard stepper drivers, and directly connected the steppers to the shield. Back then we used hobby servomotors that were connected at the place reserved for servos. (we later changed to Dynamixel and new shield almost at the same time, and Dynamixel motors directly on the RAMPS 1.4 was not really a success). Then the communication between the Arduino Mega and Raspberry Pi was I2C, which was not much stable then, you can also try with UART. That's pretty much everything you need to know about the old architecture. But note that with this architecture, you won't be able to use the current code (ROS + Arduino) that we wrote. You will need to make a lot of modifications.

RauLasH26, 2018-03-06:
Thank you for all the information. I have another request, can I buy only those 2 boards. How much will it cost me?

renarded, 2018-03-06:
You'll be able to buy those 2 boards (RPi Niryo Shield and Niryo Stepper board) after we officially release Niryo One, in about 2 months. We'll open a new store on our website so you can get every separate parts of the robot.

Stay tuned !

Closed 2018-04-03.

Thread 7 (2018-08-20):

Achat PBC board

martin73388, 2018-08-20:
Bonjour,

Quand sera t'il possible d'acheter vos custom Shield et  PCB ?
Enfin, pouvez vous donner les references de vos moteur pas à pas et celle des PCB accrochés derrière?

Merci Beaucoup et bonne continuation dans votre projet.

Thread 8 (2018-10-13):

Shield et PCB

Furansujin, 2018-10-13:
Bonjour,

Quand sera t'il possible d'acheter vos custom Shield et PCB ?

Merci Beaucoup et bonne continuation dans votre projet.

Furansujin, 2018-10-13:
ou ajouter les plans pour le fabriquer ? car sa fait longtemps qu'on attend .
sniff

renarded, 2018-10-16:
Bonjour @Furansujin,

Nous n'allons pas rendre publique les plans de fabrication des shields et PCB. Vous pouvez quand même voir la schématique globale dans le dossier "Electronics" de ce repo.

Concernant l'achat des custom Shield et PCB, nous ne proposons pas pour l'instant de les acheter à l'unité (problèmes d'organisation de production et de stock autrement). Vous pouvez toutefois acheter un Maker Kit sur notre site et vous aurez ces cartes dans le kit.

Closed 2018-10-16.

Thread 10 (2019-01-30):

What are the ratings of the stepper motors.

hemangjoshi37a, 2019-01-30:
Dear developers,

Can you please provide the rating of stepper motors used in this project??

renarded, 2019-02-04:
Hi,

You can find all specs for the stepper motors [here](https://github.com/NiryoRobotics/niryo_one/tree/master/BOM), by clicking on the Google Sheet link.

hemangjoshi37a, 2019-02-04:
I don't find any rating of motor at the link you gave me. Like is it nema
15 or 17 or 19 or is it bipolar or unipolar or anything like that...

On Mon, Feb 4, 2019, 4:25 PM Edouard Renard <notifications@github.com>
wrote:

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
--

Regards,
Hemang Joshi

renarded, 2019-02-04:
The information is on the Google sheet link on the page I provided, [here's the link](https://docs.google.com/spreadsheets/d/e/2PACX-1vRKZaMMaALGOu9jRb2pPY-hzO2wKbfK5dlxXRJX13jZtJ2pX-OD1FC3d_5NvjiSVNhvqQF9DdoSOLIK/pubhtml) to the Google Sheet.

For all NiryoSteppers we use Nema17 bipolar motors.

hemangjoshi37a, 2019-02-04:
Ok bro...

On Mon, Feb 4, 2019, 6:49 PM Edouard Renard <notifications@github.com>
wrote:

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
--

Regards,
Hemang Joshi

Closed 2019-02-04.

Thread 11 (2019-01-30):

Need gerber files for PCB.

hemangjoshi37a, 2019-01-30:
Dear Developers,

Can you please provide PCB design files like Eagle files or Gerber files so that we can make PCBs locally.

Thanl you.

renarded, 2019-02-04:
Hi,

We don't distribute, sell, or publish those files. All you can get for the custom PCB we've designed is the global overview here on GitHub.

However, all the code running on those boards is open source.

hemangjoshi37a, 2019-02-04:
Ok 😕😕

On Mon, Feb 4, 2019, 4:27 PM Edouard Renard <notifications@github.com>
wrote:

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
--

Regards,
Hemang Joshi

Closed 2019-02-04.

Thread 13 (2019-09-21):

raspberry image

marcostrullato, 2019-09-21:
Hi, I'd have a couple of questions about the software components on the raspberry.
- where can I find documentation about what's running on the raspberry image?
- do you install some proprietary software or is it just ROS?

Thanks

marcostrullato, 2019-09-21:
Ah, by the way, I have downloaded the latest image available and put into an SD as usual.
Unfortunately it doesn't boot, the screen hangs on the rainbow image.
My hardware is a raspi3.

Do you have suggestions?

Thanks

renarded, 2019-09-23:
I guess you're using a Raspberry Pi 3B+.

As for now the image is only compatible with Raspberry Pi 3B. We'll put some efforts in the future to make it compatible with version 3B+ and/or 4 (can't tell the date exactly).

As for documentation, you can find all the ROS packages [here](https://github.com/NiryoRobotics/niryo_one_ros) :)

Closed 2019-09-23.

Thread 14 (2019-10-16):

Shoulder 3D printing

MikeMihailov, 2019-10-16:
I recomend you to change holls for Shoulder_Gearing mounting: make a cone at the end of the hole. This will eliminate support inside the hole.

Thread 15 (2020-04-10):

Mechanical Part Questions

symonssoftware, 2020-04-10:
I purchased a Maker Kit and am trying to locate some of the mechanical items on the BOM but I have a couple of questions:

1. Can you tell me the bore diameter of the GT2 16 tooth gears? I measured the spindle in the stepper motors to be 5 mm but is the bore for the gear 5 mm or 6 mm?
2. Do you know a source for the 90 mm x 120 mm, Half Thrust Bearing in the United States. I can't seem to find any information on that part.

hielsnoppe, 2022-01-19:
In general, a sourcing guide for the mechanical (and electrical) parts would be really helpful. Especially since Niryo One is no longer available from the website.

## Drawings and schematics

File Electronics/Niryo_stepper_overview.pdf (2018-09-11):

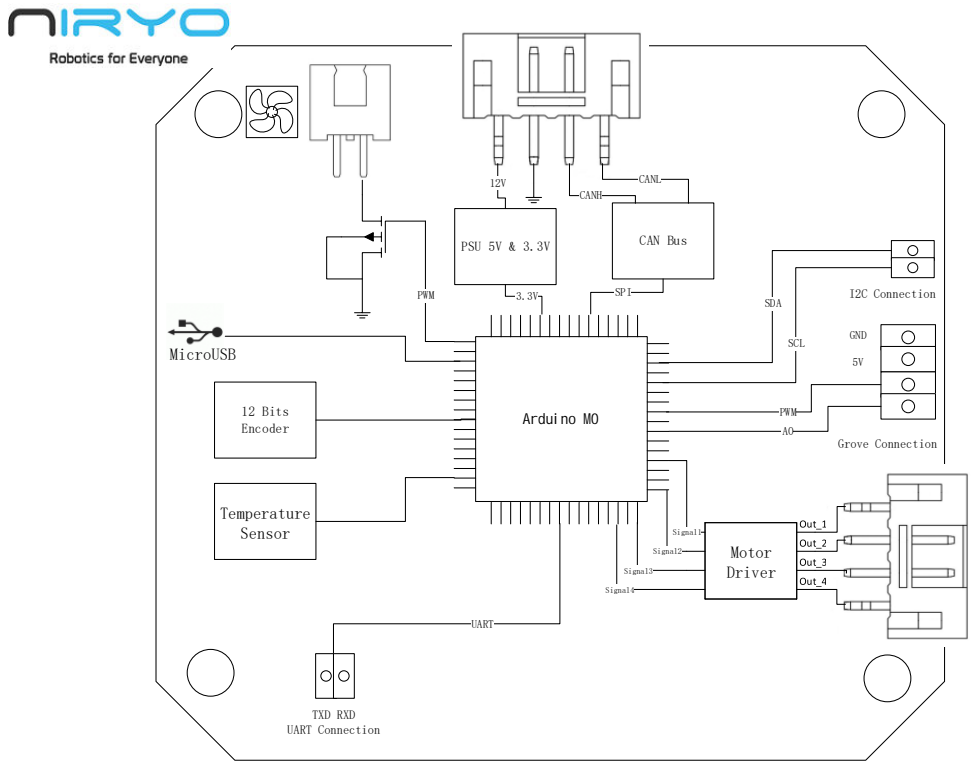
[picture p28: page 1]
Motor Driver; MicroUSB; Temperature Sensor; 12 Bits Encoder; PSU 5V & 3.3V; CAN Bus; TXD RXD UART Connection; UART; I2C Connection; Grove Connection; Signal4; Signal3; Signal2; Signal1; PWM; CANH; CANL; SPI; SCL; SDA; GND

Ardunio MK ZERO

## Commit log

2017-12-08 Add STL files
    [Air routing.STL, Arm-Bottom.STL, Arm-Top.STL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]
2018-02-05 Update arm STL files
    [Arm-Bottom.STL, Arm-Top.STL, AssemblyTools.STL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]
2018-02-05 Add tools STL files
    [EM_Main Support.STL, G1_ClampLeft.STL, G1_ClampRight.STL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]
2018-02-06 Add complete Bill of Materials
    [BOM_Niryo_One.xlsx]
2018-02-06 Add BOM for each assembly step
2018-02-07 Fix some STL files
    [Arm-Top.STL, AssemblyTool1.STL, AssemblyTool2.STL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]
2018-02-12 Fix STL files
    [Drawer-RaspberryPi.STL, Forearm-Top.STL]
2018-02-27 solve problem when axis 1 circular belt is not tight enough
    [Base.STL]
2018-04-03 BOM update
    [BOM_Niryo_One.xlsx]
2018-09-11 Hardware upgrade
    [1-Base_NiryoOne_V2.0.SLDPRT, 1-Base_NiryoOne_V2.0.STEP, 2-Shoulder_NiryoOne_V2.0.SLDPRT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]
2018-10-04 Add missing belt tensioner STL
    [Belt tensioner.STL]
2019-08-07 Update STL Files
    [AirRouting.STL, AssemblyTool1.STL, AssemblyTool2.STL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]
2020-10-08 Update base + drawer + shoulder
    [Base.STL]
